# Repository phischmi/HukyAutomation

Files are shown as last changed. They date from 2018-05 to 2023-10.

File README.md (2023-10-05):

# HukyAutomation

This is my approach on automating the Huky 500 Roaster using Artisan Software, VINT-Hardware from Phidgets and some selfmade electrics, based on an ATtiny85.
All necessary files can be found in this repository.

My goal was to automate the Huky as much as possible, but with as little effort as necessary.
Since - for the Huky - the fan has very high impact on ET and therefore BT, this was my starting point.
Furthermore it is quite tricky to change the gas stove's needle valve for a proportional control valve or to automate the installed one - which i also tried.

First i switched the Huky's original AC fan for a powerfull 12V DC fan.
To be more precise, i chose the [Noctua NF-A14 industrialPPC-3000 PWM](https://noctua.at/en/nf-a14-industrialppc-3000-pwm).
I then 3d-printed two adapter-rings to mount the fan to the original vent-bowl.
This fan (like many others) has a separate PWM-Line, which is essential for my further setup.



I wanted to controll the fan via Artisan besides the possibility to record the ET and BT.
Since version 1.2 Artisan [supports the new VINT-Phidgets](https://artisan-roasterscope.blogspot.de/2017/12/more-phidgets.html), which draw my attention to the [HUB0000](https://www.phidgets.com/?tier=3&catid=2&pcid=1&prodid=643) and the means to connect one Phidget for each of my needs.
In my case this was the [TMP1101](https://www.phidgets.com/?tier=3&catid=14&pcid=12&prodid=726) for temperature readings and the [OUT1000](https://www.phidgets.com/?tier=3&catid=2&pcid=1&prodid=711) for controlling the fan.



So, till here i was - technically - capable of displaying temperature readings in Artisan and controlling an output voltage of 0 - 4.2V utilizing Artisan's buttons and sliders.
I will outline the corresponding setup in Artisan (which is btw very simple) at the end of this article.

Next step was to convert the outputted voltage to a 5V PWM-Signal @ 20KHz.
The 20KHz are mandatorry for the fan's internal PWM-Controller to work (see [Intel's specs on 4-wire pwm controlled fans](http://www.formfactors.org/developer%5Cspecs%5Crev1_2_public.pdf)  for more information).

I did some research and it appeared to me, the simplest option available would be, to built a little circuit around an ATtiny85 MCU. 
My circuit reads the incoming voltage and converts it to the required PWM-Signal.
Furthermore it powers the 12V fan. The MCU itself is powered by 5V from 7805 IC, which is sourced by the same 12V as the fan.
I'm not an electrician and this is virtually my first self-made circuit - hence kept very simple and stripped-down.







The final step was to configure Artisan to read the temperature recordings and to control the fan.
This is easily done by selecting the `TMP1101` under `Extras >> Devices >> ET/BT` and by creating a slider with the following settings. 



As `Action` i chose `VOUT Command` and `Command` is `out(n,{})`, with 'n' = channel '0' (in my case). `Factor` is set to `0.042`, since the maximum output is 100 * 0.042 = 4.2 Volts.

I also created a bunch of buttons to set the slider to some pre-configured values, e.g. Off, 60%, 80%, 100% (this range works quite well for me). Syntax is the same as for the slider.



As said before, the fan and therefore convection has a high impact on the Huky's ET.
The above setup can therefore easily be used with Artisan's software PID to hold a certain temperature, e.g. for warming up the whole roaster or in between roasts.

For those interested and german-speaking, [this](https://roboternetz.de/community/threads/71926-Einfache-ATtiny-basierte-spannungsgesteuerte-L%C3%BCfter-Regelung) is the topic in german "Roboternetz", where the circuit was planned. Many thanks to those people over there, who helped me a lot!
<!--stackedit_data:
eyJoaXN0b3J5IjpbLTE4MzkwMDMzNzUsMzk0NTEwMTI3LC0xOT
Q1MzU3MTQ4LC0yMDM2ODYzMTgwLC0zMjUzNjU5NDQsNDM4NDM4
NzQ2LC00NjI4NDUwMTldfQ==
-->

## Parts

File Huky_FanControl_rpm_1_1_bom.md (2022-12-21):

| Ammount | Part Type | Properties |
|---|---|---|
|4			|Capacitor  |100nF |
|1			|Capacitor  |330nF |
|1			|Electrolytic Capacitor  |1µF|
|3			|Resistor |10kΩ |
|1			|Diode		  |1N4002 |
|1			|ATiny85 | |
|2			|Screw Terminal |4 pins|
|1			|Voltage Regulator - 5V  |LM7805|
|1			|Pushbutton | |

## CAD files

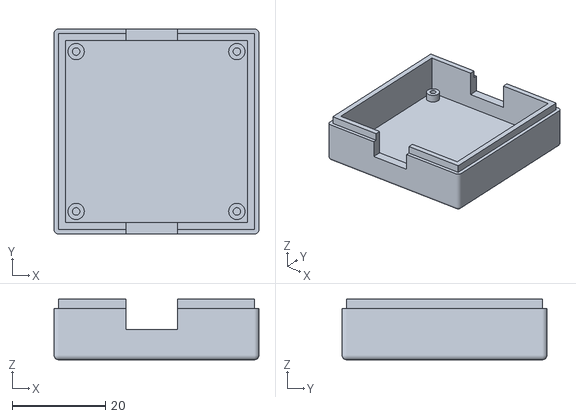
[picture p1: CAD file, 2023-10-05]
Huky_FanControl_Case_Bottom.stl
44.0 x 44.0 x 13.0

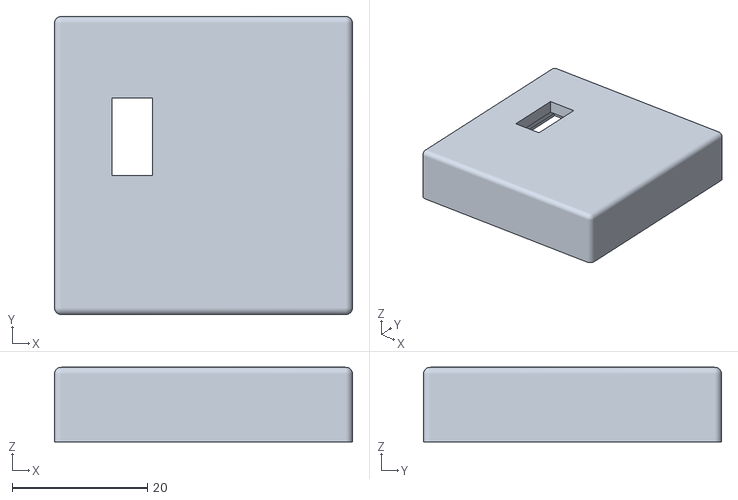
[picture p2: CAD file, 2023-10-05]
Huky_FanControl_Case_Top.stl
44.0 x 44.0 x 11.0

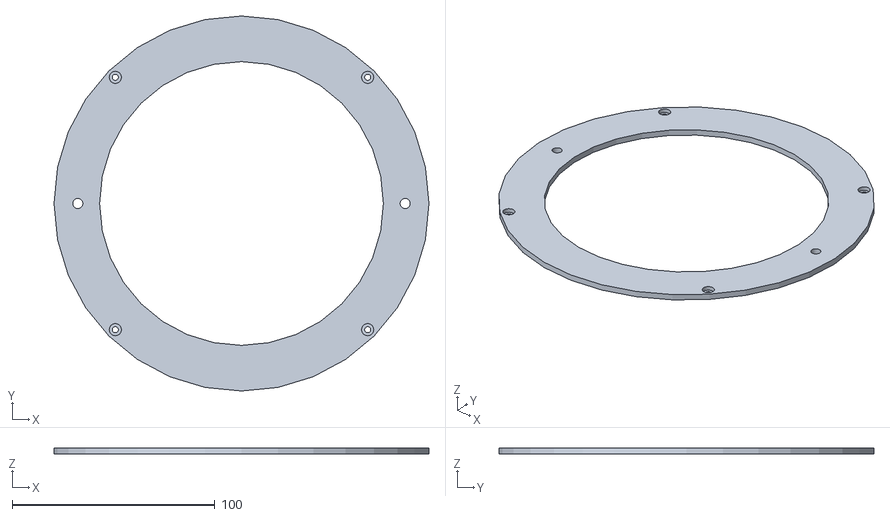
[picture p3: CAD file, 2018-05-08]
HukyAdapterBottom.stl
185.0 x 185.0 x 3.00

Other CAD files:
HukyAdapterTop.stl

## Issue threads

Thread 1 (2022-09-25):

circuit board availability

rfsch, 2022-09-25:
hello

where can the circuit board and the necessary components be purchased ?

Thanks

Joe

phischmi, 2023-10-04:
The circuit board must be printed and assembled by yourself. I do not have any boards in stock.

phischmi, 2023-10-04:
The circuit board must be printed and assembled by yourself. I do not have any boards in stock.

Closed 2023-10-04.

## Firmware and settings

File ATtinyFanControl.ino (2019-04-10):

/*

*/

void setup() {
  // Set 64MHz asynchronus clock mode, if bits not already set by Bootloader
  PLLCSR |= (1 << PLLE);            // PLL Enable
  while(!(PLLCSR & (1 << PLOCK)));  // PLL Lock Detector
  PLLCSR |= (1 << PCKE);            // PCK Enable
  
  // Set PWM frequency to (64MHz / 16) / (199 + 1) = 20KHz
  TCCR1 =   
            (1 << PWM1A)  |   // Pulse Width Modulator A Enable
            (1 << COM1A1) |   // Comparator A Output Mode to OC1x cleared on compare match. Set when TCNT1 = $00; Inverted Output not connected
            (1 << CS12)   |   // Set Prescaler to 0101 = 16
            (1 << CS10);      // Set Prescaler to 0101 = 16
  
  OCR1C = 199;                // Set Top-Value to 199
  OCR1A = 0;                  // Set initial value to 0
  
  pinMode(1, OUTPUT);         // Set digital pin 1 (PB1) to OUTPUT
}

void loop() {
  OCR1A = map(analogRead(A2), 0, 851, 0, 199); // 851 equals ~4.2 Volts
}

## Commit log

2019-04-10 Added an additional resistor to ATtiny's AnalogInput
    [Huky_FanControl_rpm_1_1.fzz]
2019-08-08 Changed pictures and added circuit diagram
2019-12-30 Updated schematic to v.1.1
2020-02-18 Deleted old version of the circuit
    [Huky_FanControl_rpm.fzz]
2021-03-23 Added Gerber-Files for production
    Additional Gerber-Files for production without Fritzing
2021-03-31 Update README.md
    Updated circuit diagram
2022-12-21 Added bom to repo
2022-12-21 Added bom
2023-10-05 Added a 3D printable case for the FanControl Rev. 1.1
    [Huky_FanControl_Case_Bottom.3mf, Huky_FanControl_Case_Top.3mf]
2023-10-05 Added a 3D printable Case for FanControl Rev. 1.1
    [Huky_FanControl_Case_Bottom.stl, Huky_FanControl_Case_Top.stl]
2023-10-05 Delete Huky_FanControl_Case_Bottom.3mf
    Instead added STL file
    [Huky_FanControl_Case_Bottom.3mf]
2023-10-05 Delete Huky_FanControl_Case_Top.3mf
    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
    [Huky_FanControl_Case_Top.3mf]
